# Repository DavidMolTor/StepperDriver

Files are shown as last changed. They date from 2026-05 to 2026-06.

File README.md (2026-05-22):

# STEPPER DRIVER

A simple stepper driver module using a Seeed Studio Xiao development board and TMC2209 stepper driver IC.

## Introduction

This module is designed to be used as a stepper controller for a testbench platform.

The design is centered around the ESP32-C6 XIAO development board from Seeed Studio. It can be soldered as an SMD part in order to have access to the driver debug wire and JTAG connector on the board.

Compatibility with other drivers like the TMC2208 could be possible, the footprints for the different package needs to be checked before attempting to use it.

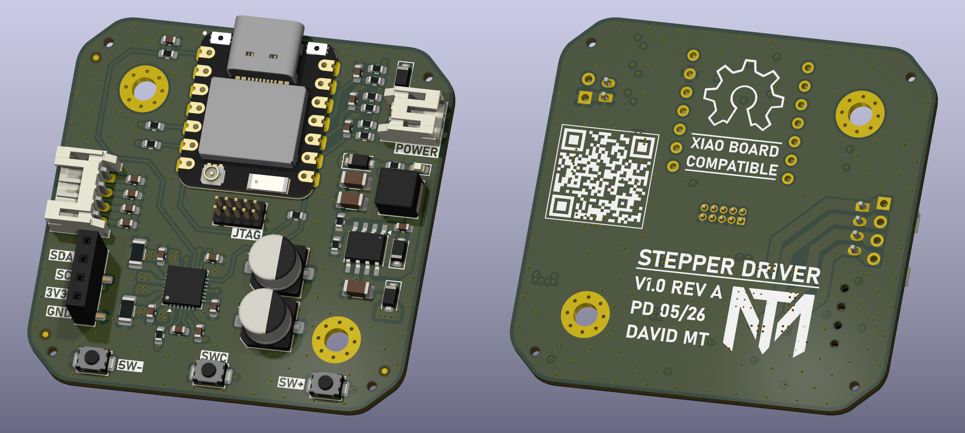
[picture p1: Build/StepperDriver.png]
STEPPER DRIVER


## Features

 - Wide input voltage range of 12-28V.

 - High current capability of up to 2.0A.

 - Wireless connectivity and LCD screen.

 - Afforable BOM with high quality parts.

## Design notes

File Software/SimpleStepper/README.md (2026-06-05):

| Supported Targets | ESP32-C6 |
| --- | --- |

# Simple Stepper Driver

Simple stepper driver using the TMC2209 in UART-controlled mode.

### Hardware Required

* XIAO ESP32-C6 development board
* TMC2209 stepper motor driver

### Configure the Project

TODO

### Build and Flash

Run `idf.py -p PORT flash monitor` to build, flash and monitor the project.

(To exit the serial monitor, type ``Ctrl-]``.)

See the [Getting Started Guide](https://docs.espressif.com/projects/esp-idf/en/latest/get-started/index.html) for full steps to configure and use ESP-IDF to build projects.

## Example Output

TODO

## Troubleshooting

TODO

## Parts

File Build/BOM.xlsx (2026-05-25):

Reference | Qty | Value | Footprint | Manufacturer Part | JLCPCB Part
C1,C2,C3,C8,C12,C13,C14,C15 | 8 | 100n | Capacitor_SMD:C_0603_1608Metric | CC0603KRX7R9BB104 | C14663
C4,C5 | 2 | 47u | Capacitor_SMD:CP_Elec_6.3x5.8 | SVZ1VM470E06E00RAXXX | C721322
C6,C18,C19,C20 | 4 | 10n | Capacitor_SMD:C_0603_1608Metric | 0603B103K500NT | C57112
C7 | 1 | 10u | Capacitor_SMD:C_1206_3216Metric | CL31A106KBHNNNE | C13585
C9,C10 | 2 | 22u | Capacitor_SMD:C_1206_3216Metric | CL31A226KAHNNNE | C12891
C11 | 1 | 22n | Capacitor_SMD:C_0603_1608Metric | CL10B223KB8NNNC | C21122
C16 | 1 | 2.2u | Capacitor_SMD:C_0603_1608Metric | CL10A225KO8NNNC | C23630
C17 | 1 | 1u | Capacitor_SMD:C_0603_1608Metric | CL10A105KB8NNNC | C15849
D1,D2,D4 | 3 | DSK24 | Diode_SMD:D_SOD-123F | DSK24 | C22466352
D3 | 1 | SMF40CA | Diode_SMD:D_SOD-123F | SMF40CA | C42371749
D5 | 1 | RED | LED_SMD:LED_0603_1608Metric | KT-0603R | C2286
L1 | 1 | 47u | Inductor_SMD:L_Changjiang_FNR5040S | FNR5040S470MT | C167974
R1,R3,R10,R11,R12,R14,R15,R16 | 8 | 10K | Resistor_SMD:R_0603_1608Metric | 0603WAF1002T5E | C25804
R2 | 1 | 3.3K | Resistor_SMD:R_0603_1608Metric | 0603WAF3301T5E | C22978
R4 | 1 | 22K | Resistor_SMD:R_0603_1608Metric | 0603WAF2202T5E | C31850
R5,R6 | 2 | 100m | Resistor_SMD:R_1206_3216Metric | 1206W4F100LT5E | C25334
R7,R8,R13 | 3 | 2.2K | Resistor_SMD:R_0603_1608Metric | 0603WAF2201T5E | C4190
R9 | 1 | 0R | Resistor_SMD:R_0603_1608Metric | 0603WAF0000T5E | C21189
SW1,SW2,SW3 | 3 | SPST_TS | Button_Switch_SMD:SW_SPST_TS-1088-xR020 | TS-1088-AR02016 | C720477
U1 | 1 | TPS5430DDA | Custom_Parts:TI_SO-PowerPAD-8_ThermalVias | TPS5430DDAR | C9864
U2 | 1 | TMC2209-LA | Custom_Parts:VQFN-28-1EP_5x5mm_P0.5mm_EP3.7x3.7mm_ThermalVias | TMC2209-LA-T | C2150710

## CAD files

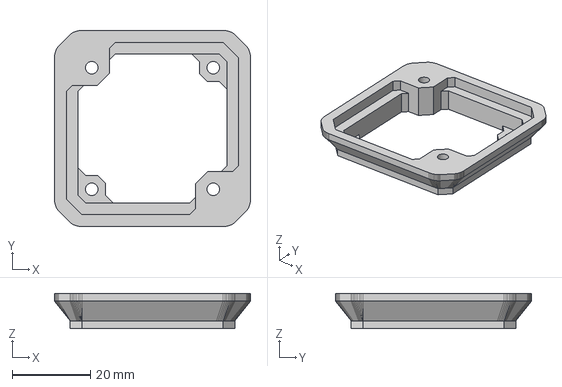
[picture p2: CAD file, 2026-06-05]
Build/Spacer.step
50.0 x 50.0 x 9.00 mm

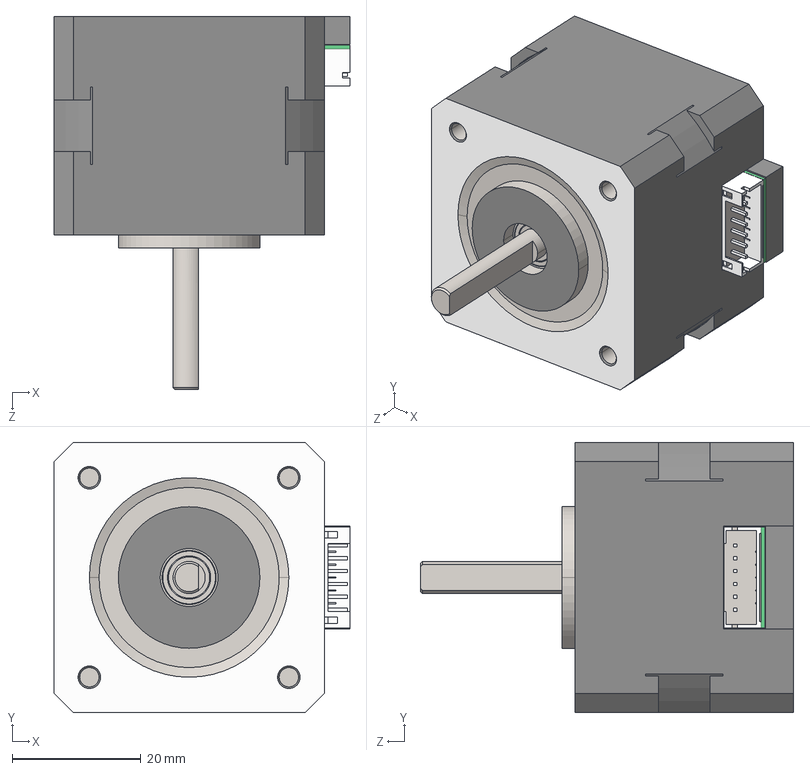
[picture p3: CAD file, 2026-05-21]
Build/Nema17.step
46.0 x 42.0 x 58.0 mm

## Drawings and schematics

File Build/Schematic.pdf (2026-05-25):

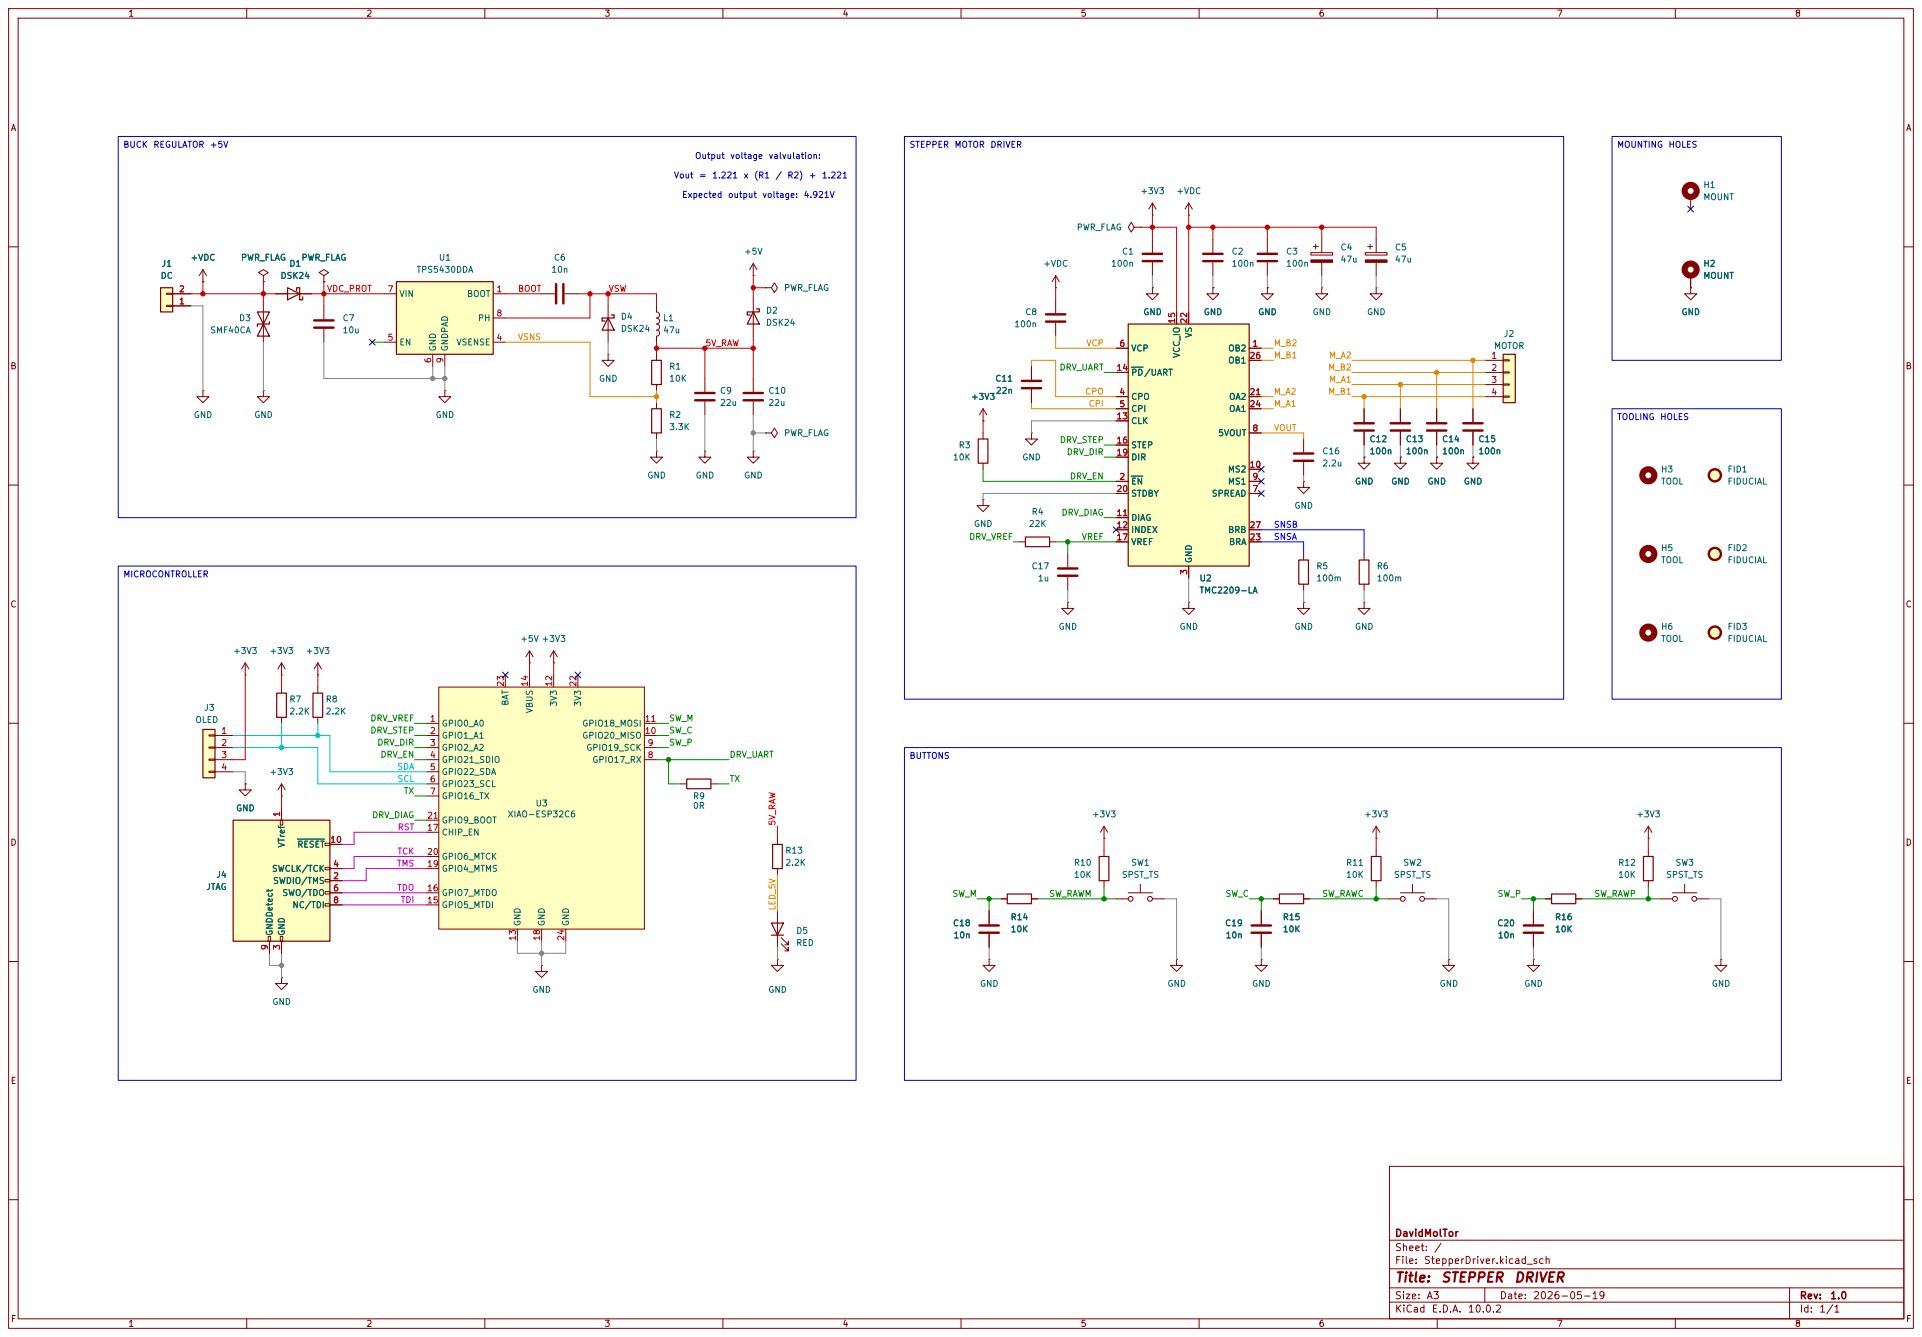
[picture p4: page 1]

Size: A3 | Rev: 1.0 | F Date: 2026-05-19
KiCad E.D.A. 10.0.2 | Id: 1/1

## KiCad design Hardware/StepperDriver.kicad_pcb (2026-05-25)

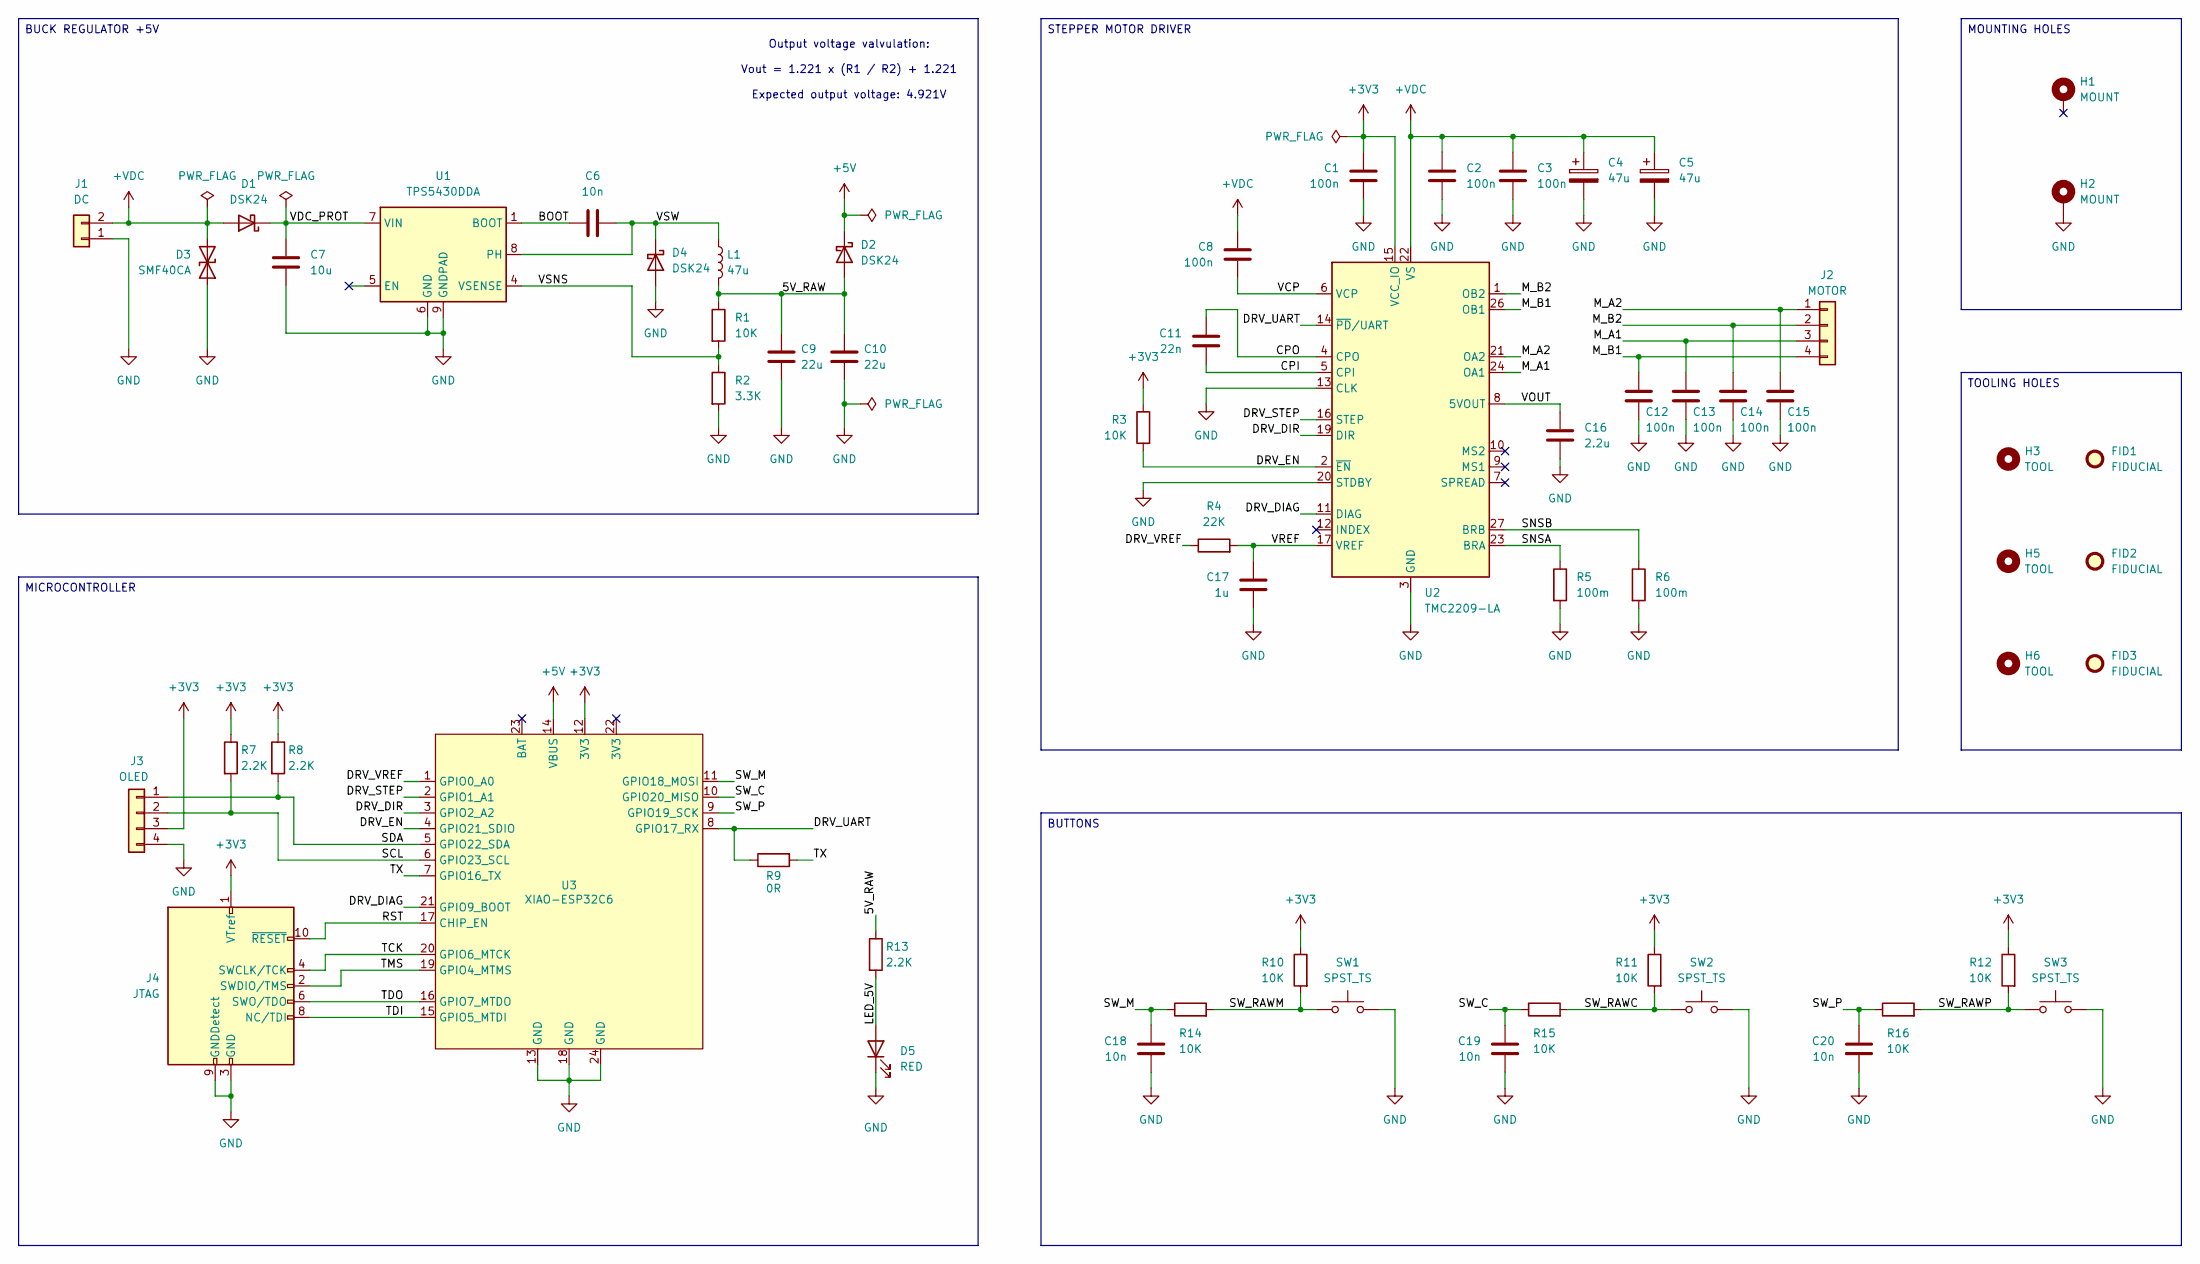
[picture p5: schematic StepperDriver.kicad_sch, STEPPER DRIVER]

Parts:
C1, C2, C3, C8, C12, C13, C14, C15: 100n; C_0603_1608Metric; Manufacturer Part CC0603KRX7R9BB104; JLCPCB Part C14663
C4, C5: 47u; CP_Elec_6.3x5.8; Manufacturer Part SVZ1VM470E06E00RAXXX; JLCPCB Part C721322
C6, C18, C19, C20: 10n; C_0603_1608Metric; Manufacturer Part 0603B103K500NT; JLCPCB Part C57112
C7: 10u; C_1206_3216Metric; Manufacturer Part CL31A106KBHNNNE; JLCPCB Part C13585
C9, C10: 22u; C_1206_3216Metric; Manufacturer Part CL31A226KAHNNNE; JLCPCB Part C12891
C11: 22n; C_0603_1608Metric; Manufacturer Part CL10B223KB8NNNC; JLCPCB Part C21122
C16: 2.2u; C_0603_1608Metric; Manufacturer Part CL10A225KO8NNNC; JLCPCB Part C23630
C17: 1u; C_0603_1608Metric; Manufacturer Part CL10A105KB8NNNC; JLCPCB Part C15849
D1, D2, D4: DSK24; D_SOD-123F; Manufacturer Part DSK24; JLCPCB Part C22466352
D3: SMF40CA; D_SOD-123F; Manufacturer Part SMF40CA; JLCPCB Part C42371749
D5: RED; LED_0603_1608Metric; Manufacturer Part KT-0603R; JLCPCB Part C2286
FID1, FID2, FID3: FIDUCIAL; Fiducial_0.75mm_Mask1.5mm
H1, H2: MOUNT; MountingHole_3.2mm_M3_Pad_Via
H3, H5, H6: TOOL; ToolingHole_1.152mm
J1: DC; JST_PH_S2B_1x02_COMBO; Manufacturer Part S2B-PH-K(LF)(SN); JLCPCB Part C265016
J2: MOTOR; JST_PH_S4B_1x04_COMBO; Manufacturer Part S4B-PH-K(LF)(SN); JLCPCB Part C265452
J3: OLED; HEADER_THROUGH_1x04_P2.54mm
J4: JTAG; PinHeader_2x05_P1.27mm_Vertical
L1: 47u; L_Changjiang_FNR5040S; Manufacturer Part FNR5040S470MT; JLCPCB Part C167974
R1, R3, R10, R11, R12, R14, R15, R16: 10K; R_0603_1608Metric; Manufacturer Part 0603WAF1002T5E; JLCPCB Part C25804
R2: 3.3K; R_0603_1608Metric; Manufacturer Part 0603WAF3301T5E; JLCPCB Part C22978
R4: 22K; R_0603_1608Metric; Manufacturer Part 0603WAF2202T5E; JLCPCB Part C31850
R5, R6: 100m; R_1206_3216Metric; Manufacturer Part 1206W4F100LT5E; JLCPCB Part C25334
R7, R8, R13: 2.2K; R_0603_1608Metric; Manufacturer Part 0603WAF2201T5E; JLCPCB Part C4190
R9: 0R; R_0603_1608Metric; Manufacturer Part 0603WAF0000T5E; JLCPCB Part C21189
SW1, SW2, SW3: SPST_TS; SW_SPST_TS-1088-xR020; Manufacturer Part TS-1088-AR02016; JLCPCB Part C720477
U1: TPS5430DDA; TI_SO-PowerPAD-8_ThermalVias; Manufacturer Part TPS5430DDAR; JLCPCB Part C9864
U2: TMC2209-LA; VQFN-28-1EP_5x5mm_P0.5mm_EP3.7x3.7mm_ThermalVias; Manufacturer Part TMC2209-LA-T; JLCPCB Part C2150710
U3: XIAO-ESP32C6; XIAO-ESP32C6-SMD

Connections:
+3V3: C1.1, J3.3, J4.1 (VTref), R3.1, R7.1, R8.1, R10.1, R11.1, R12.1, U2.15 (VCC_IO), U3.12 (3V3)
+5V: D2.1 (K), U3.14 (VBUS)
+VDC: C2.1, C3.1, C4.1, C5.1, C8.1, D1.2 (A), D3.2 (A2), J1.2, U2.22 (VS), U2.28 (VS)
/5V_RAW: C9.1, C10.1, D2.2 (A), L1.2, R1.1, R13.1
/BOOT: C6.1, U1.1 (BOOT)
/CPI: C11.2, U2.5 (CPI)
/CPO: C11.1, U2.4 (CPO)
/DRV_DIAG: U2.11 (DIAG), U3.21 (GPIO9_BOOT)
/DRV_DIR: U2.19 (DIR), U3.3 (GPIO2_A2)
/DRV_EN: R3.2, U2.2 (~EN), U3.4 (GPIO21_SDIO)
/DRV_STEP: U2.16 (STEP), U3.2 (GPIO1_A1)
/DRV_UART: R9.1, U2.14 (~PD/UART), U3.8 (GPIO17_RX)
/DRV_VREF: R4.1, U3.1 (GPIO0_A0)
/LED_5V: D5.2 (A), R13.2
/M_A1: C13.1, J2.3, U2.24 (OA1)
/M_A2: C15.1, J2.1, U2.21 (OA2)
/M_B1: C12.1, J2.4, U2.26 (OB1)
/M_B2: C14.1, J2.2, U2.1 (OB2)
/RST: J4.10 (~RESET), U3.17 (CHIP_EN)
/SCL: J3.2, R7.2, U3.6 (GPIO23_SCL)
/SDA: J3.1, R8.2, U3.5 (GPIO22_SDA)
/SNSA: R5.1, U2.23 (BRA)
/SNSB: R6.1, U2.27 (BRB)
/SW_C: C19.1, R15.1, U3.10 (GPIO20_MISO)
/SW_M: C18.1, R14.1, U3.11 (GPIO18_MOSI)
/SW_P: C20.1, R16.1, U3.9 (GPIO19_SCK)
/SW_RAWC: R11.2, R15.2, SW2.1
/SW_RAWM: R10.2, R14.2, SW1.1
/SW_RAWP: R12.2, R16.2, SW3.1
/TCK: J4.4 (SWCLK/TCK), U3.20 (GPIO6_MTCK)
/TDI: J4.8 (NC/TDI), U3.15 (GPIO5_MTDI)
/TDO: J4.6 (SWO/TDO), U3.16 (GPIO7_MTDO)
/TMS: J4.2 (SWDIO/TMS), U3.19 (GPIO4_MTMS)
/TX: R9.2, U3.7 (GPIO16_TX)
/VCP: C8.2, U2.6 (VCP)
/VDC_PROT: C7.1, D1.1 (K), U1.7 (VIN)
/VOUT: C16.1, U2.8 (5VOUT)
/VREF: C17.1, R4.2, U2.17 (VREF)
/VSNS: R1.2, R2.1, U1.4 (VSENSE)
/VSW: C6.2, D4.1 (K), L1.1, U1.8 (PH)
GND: C1.2, C2.2, C3.2, C4.2, C5.2, C7.2, C9.2, C10.2, C12.2, C13.2, C14.2, C15.2, C16.2, C17.2, C18.2, C19.2, C20.2, D3.1 (A1), D4.2 (A), D5.1 (K), H2.1 (1_1), J1.1, J3.4, J4.3 (GND), J4.5 (GND), J4.9 (GNDDetect), R2.2, R5.2, R6.2, SW1.2, SW2.2, SW3.2, U1.6 (GND), U1.9 (GNDPAD), U2.3 (GND), U2.13 (CLK), U2.18 (GND), U2.20 (STDBY), U2.29 (GND), U3.13 (GND), U3.18 (GND), U3.24 (GND)

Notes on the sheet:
Output voltage valvulation: Vout = 1.221 x (R1 / R2) + 1.221 Expected output voltage: 4.921V
TOOLING HOLES
MICROCONTROLLER
MOUNTING HOLES
BUTTONS
BUCK REGULATOR +5V
STEPPER MOTOR DRIVER

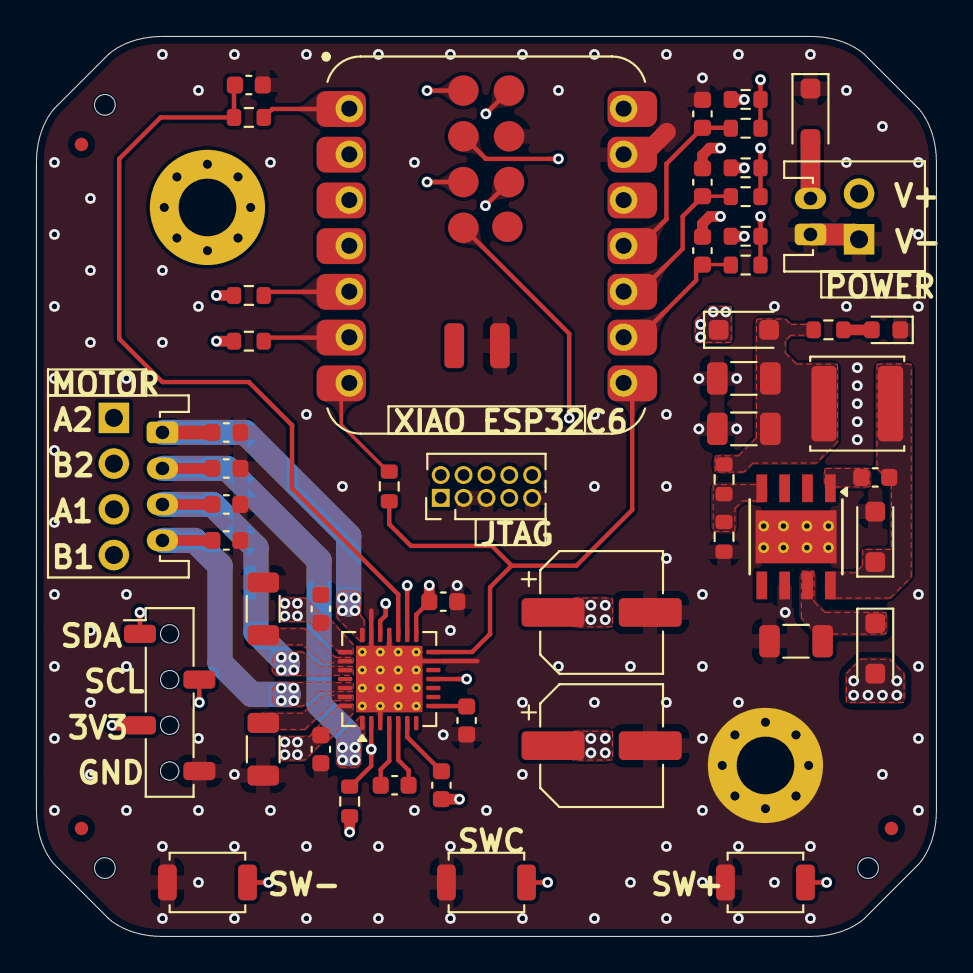
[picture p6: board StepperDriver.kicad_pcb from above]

Board: 6 copper layers, 50.0 x 50.0 mm, 60 parts (0 on the bottom side), 41 nets.

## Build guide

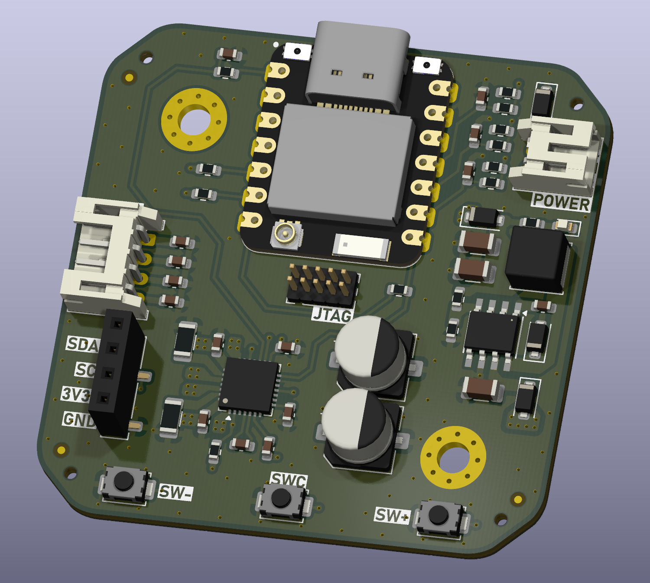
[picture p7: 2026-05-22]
Build/Front.png

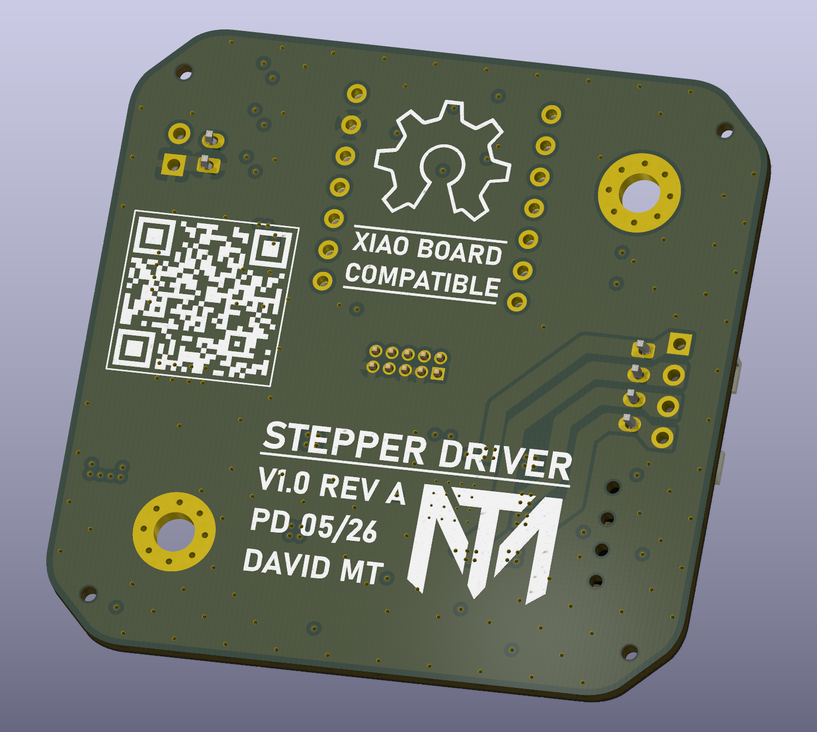
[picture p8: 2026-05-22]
Build/Back.png

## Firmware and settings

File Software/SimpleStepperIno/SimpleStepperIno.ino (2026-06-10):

#include <TMC2209.h>

// Instantiate TMC2209 driver
TMC2209 stepper_driver;

// Serial stream object declaration
HardwareSerial& serial_stream = Serial0;

// Stepper driver UART definitions
#define UART_SERIAL_PORT  TMC2209::SERIAL_ADDRESS_0
#define UART_BAUD_RATE    115200
#define UART_RX_PIN       17
#define UART_TX_PIN       16

// Stepper driver pin definitions
#define STP_PIN   1
#define DIR_PIN   2
#define EN_PIN    21

// TMC2209 current control definitions
#define RMS_CURRENT_VALUE   200.0f
#define EXT_RESISTOR_VALUE  0.1f

// Value definitions for the NEMA17
#define STEPS_PER_REV       200.0f
#define MAX_RPM             600.0f
#define RPM_STEPPING        60.0f
#define MAX_USTEPS          8

// GPIO pin definitions
#define SWM_PIN 18
#define SWC_PIN 20
#define SWP_PIN 19

static uint32_t step_delay_us     = 0;
static uint8_t current_microstep  = 0;

static float current_speed_rpm    = 0.0f;
static float target_speed_rpm     = 60.0f;
static float accel_rpm_per_s      = 15.0f;

static long last_ramp_update      = 0;

static uint32_t rpm_to_step_delay_us(float rpm, uint8_t microstep) {
  if (rpm <= 0.0f) {
    return 0;
  }

  if (rpm > MAX_RPM) {
    rpm = MAX_RPM;
  }

  float steps_per_rev = STEPS_PER_REV * (float)(2 ^ microstep);
  float steps_per_sec = (rpm * steps_per_rev) / 60.0f;

  if (steps_per_sec < 1.0f) {
    steps_per_sec = 1.0f;
  }

  return (uint32_t)(1000000.0f / steps_per_sec);
}

static void stepper_apply_speed() {
  step_delay_us = rpm_to_step_delay_us(current_speed_rpm, current_microstep);
}

static void stepper_set_direction(bool clockwise) {
  digitalWrite(DIR_PIN, clockwise ? HIGH : LOW);
}

static void stepper_set_speed_rpm(float rpm) {
  if (rpm < 0.0f) {
    rpm = 0.0f;
  }

  if (rpm > MAX_RPM) {
    rpm = MAX_RPM;
  }

  target_speed_rpm = rpm;
}

static void stepper_set_acceleration_rpm(float rpm_per_s) {
  if (rpm_per_s < 1.0f) {
    rpm_per_s = 1.0f;
  }

  accel_rpm_per_s = rpm_per_s;
}

static void stepper_update_speed_ramp(void) {
  long now = micros();
  int64_t dt_us = now - last_ramp_update;
  last_ramp_update = now;

  if (dt_us <= 0) {
    return;
  }

  float dt_s = (float)dt_us / 1000000.0f;
  float max_delta_rpm = accel_rpm_per_s * dt_s;
  float error = target_speed_rpm - current_speed_rpm;

  if (fabsf(error) <= max_delta_rpm) {
    current_speed_rpm = target_speed_rpm;
  } else if (error > 0.0f) {
    current_speed_rpm += max_delta_rpm;
  } else {
    current_speed_rpm -= max_delta_rpm;
  }

  stepper_apply_speed();
}

static void stepper_run(void) {
  stepper_update_speed_ramp();

  if (step_delay_us == 0) {
    delayMicroseconds(1000);
    return;
  }

  digitalWrite(STP_PIN, HIGH);
  delayMicroseconds(2);
  digitalWrite(STP_PIN, LOW);

  if (step_delay_us > 2) {
    delayMicroseconds(step_delay_us - 2);
  }
}

static void gpioCallback() {
  if (digitalRead(SWM_PIN) == LOW) {
    target_speed_rpm -= RPM_STEPPING;

    if (target_speed_rpm < 0.0f)
      target_speed_rpm = 0;
  }

  if (digitalRead(SWC_PIN) == LOW) {
    current_microstep++;

    if (current_microstep > MAX_USTEPS)
      current_microstep = 0;
  }

  if (digitalRead(SWP_PIN) == LOW) {
    target_speed_rpm += RPM_STEPPING;

    if (target_speed_rpm > MAX_RPM)
      target_speed_rpm = MAX_RPM;
  }

  stepper_set_speed_rpm(target_speed_rpm);
  stepper_apply_speed();

  Serial.print("Motor speed / microsteps: ");
  Serial.print(target_speed_rpm);
  Serial.print(" / ");
  Serial.println(current_microstep);
}

void setup() {
  // Set the step pin configuration
  pinMode(STP_PIN, OUTPUT);
  digitalWrite(STP_PIN, LOW);

  // Set the direction pin configuration
  pinMode(DIR_PIN, OUTPUT);
  digitalWrite(DIR_PIN, LOW);

  // Set the enable pin configuration
  pinMode(EN_PIN, OUTPUT);
  digitalWrite(EN_PIN, LOW);

  // Set the switch configurations
  pinMode(SWM_PIN, INPUT);
  pinMode(SWC_PIN, INPUT);
  pinMode(SWP_PIN, INPUT);
  attachInterrupt(digitalPinToInterrupt(SWM_PIN), gpioCallback, FALLING);
  attachInterrupt(digitalPinToInterrupt(SWC_PIN), gpioCallback, FALLING);
  attachInterrupt(digitalPinToInterrupt(SWP_PIN), gpioCallback, FALLING);

  delay(100);

  // Initialize the serial port
  Serial.begin(UART_BAUD_RATE);
  delay(100);

  // Setup the TMC2209 stepper driver
  stepper_driver.setup(serial_stream, UART_BAUD_RATE, UART_SERIAL_PORT, UART_RX_PIN, UART_TX_PIN);
  delay(100);

  // CHeck if the driver is setup and working
  if (stepper_driver.isSetupAndCommunicating()) {
    // Enable the stepper driver
    stepper_driver.enable();

    // Set the initial configuration
    stepper_driver.useExternalSenseResistors();
    stepper_driver.enableCoolStep();
    stepper_driver.setMicrostepsPerStep(current_microstep);

    // Set the current control configuration
    stepper_driver.setRMSCurrent(RMS_CURRENT_VALUE, EXT_RESISTOR_VALUE);
    stepper_driver.enableAutomaticCurrentScaling();
    stepper_driver.enableAutomaticGradientAdaptation();

    // Set the initial direction
    stepper_set_direction(true);

    // Set the initial update time
    last_ramp_update = micros();

    Serial.println("Stepper driver running...");
  } else {
    Serial.println("Stepper driver setup error!");
  }
}

void loop() {
  // Execute the stepper control
  stepper_run();
}

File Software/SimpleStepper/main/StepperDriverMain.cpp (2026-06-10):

#include <cstdio>
#include <cstring>

#include "freertos/FreeRTOS.h"
#include "freertos/task.h"

#include "driver/gpio.h"
#include "driver/usb_serial_jtag.h"
#include "driver/usb_serial_jtag_vfs.h"

#include "sdkconfig.h"

#include "ManagerWifi.h"
#include "ManagerOTA.h"

#include "TMC2209.h"

// User accessible LED GPIO definition
#define USER_LED_GPIO (gpio_num_t)CONFIG_USER_LED_GPIO

// TMC2209 driver pin definitions
#define TMC2209_VREF_GPIO    (gpio_num_t)CONFIG_TMC2209_VREF_GPIO
#define TMC2209_STEP_GPIO    (gpio_num_t)CONFIG_TMC2209_STEP_GPIO
#define TMC2209_DIR_GPIO     (gpio_num_t)CONFIG_TMC2209_DIR_GPIO
#define TMC2209_EN_GPIO      (gpio_num_t)CONFIG_TMC2209_EN_GPIO
#define TMC2209_RX_GPIO      (gpio_num_t)CONFIG_TMC2209_RX_GPIO
#define TMC2209_TX_GPIO      (gpio_num_t)CONFIG_TMC2209_TX_GPIO
#define TMC2209_DIAG_GPIO    (gpio_num_t)CONFIG_TMC2209_DIAG_GPIO

// TMC2209 serial address definition
#define TMC2209_SERIAL_ADDRESS 0

// I2C bus pin definitions
#define I2C_SDA_GPIO CONFIG_I2C_SDA_GPIO
#define I2C_SCL_GPIO CONFIG_I2C_SCL_GPIO

// Board switches pin definitions
#define SWM_GPIO CONFIG_SWM_GPIO
#define SWC_GPIO CONFIG_SWC_GPIO
#define SWP_GPIO CONFIG_SWP_GPIO

// NEMA17 specification definitions
#define STEPS_PER_REV   200
#define CURRENT_RMS_MA  1000

static void init_console()
{
    usb_serial_jtag_driver_config_t cfg = {
        .tx_buffer_size = 256,
        .rx_buffer_size = 256,
    };
    ESP_ERROR_CHECK(usb_serial_jtag_driver_install(&cfg));

    usb_serial_jtag_vfs_use_driver();

    usb_serial_jtag_vfs_set_rx_line_endings(ESP_LINE_ENDINGS_CR);
    usb_serial_jtag_vfs_set_tx_line_endings(ESP_LINE_ENDINGS_CRLF);

    setvbuf(stdin, NULL, _IONBF, 0);
    setvbuf(stdout, NULL, _IONBF, 0);
    setvbuf(stderr, NULL, _IONBF, 0);
}

static void init_gpio()
{
    // Configure the user LED
    gpio_reset_pin(USER_LED_GPIO);
    gpio_set_direction(USER_LED_GPIO, GPIO_MODE_OUTPUT);
    gpio_set_level(USER_LED_GPIO, 1);

    // Default button configuration
    gpio_config_t io_conf = {
        .pin_bit_mask   = 1ULL,
        .mode           = GPIO_MODE_INPUT,
        .pull_up_en     = GPIO_PULLUP_DISABLE,
        .pull_down_en   = GPIO_PULLDOWN_DISABLE,
        .intr_type      = GPIO_INTR_DISABLE
    };

    // Configure each button
    io_conf.pin_bit_mask = 1ULL << CONFIG_SWM_GPIO;
    ESP_ERROR_CHECK(gpio_config(&io_conf));
    io_conf.pin_bit_mask = 1ULL << CONFIG_SWC_GPIO;
    ESP_ERROR_CHECK(gpio_config(&io_conf));
    io_conf.pin_bit_mask = 1ULL << CONFIG_SWP_GPIO;
    ESP_ERROR_CHECK(gpio_config(&io_conf));    
}

static void run_maintenance(ManagerWifi &wifi, ManagerOTA &ota)
{
    ota.startServiceMDNS();
    ota.startWebServer();

    while (true) {
        printf("OTA web server active, waiting for firmware...\n");
        vTaskDelay(pdMS_TO_TICKS(1000));
    }
}

static void run_app(ManagerWifi &wifi)
{
    TMC2209 stepper_driver;

    stepper_driver.setGPIO(TMC2209_EN_GPIO, TMC2209_STEP_GPIO, TMC2209_DIR_GPIO);
    vTaskDelay(pdMS_TO_TICKS(100));

    stepper_driver.setup(UART_NUM_0, TMC2209_TX_GPIO, TMC2209_RX_GPIO, TMC2209_SERIAL_ADDRESS);
    vTaskDelay(pdMS_TO_TICKS(100));
    
    while (true) {
        printf("Driver status: %d\n", stepper_driver.getConnected());
        printf("Main app running...\n");
        vTaskDelay(pdMS_TO_TICKS(10000));
    }
}

extern "C" void app_main(void)
{
    init_console();
    init_gpio();

    // Manager definitions
    ManagerWifi managerWifi;
    ManagerOTA managerOTA(SWC_GPIO, USER_LED_GPIO);

    // Check for OTA button
    bool ota_mode = managerOTA.isOtaButtonPressed();

    // Initialize the wifi
    managerWifi.init();

    // Check for saved credentials
    ManagerWifi::Credentials credentials;
    do
    {
        if (!managerWifi.hasSavedCredentials()) {
            credentials = managerWifi.serialProvisioning();
        } else {
            credentials = managerWifi.loadCredentials();
        }
    } while (!credentials.valid());

    // Connect to the given wifi network
    if (!managerWifi.connect(credentials) && ota_mode) {
        do
        {
            credentials = managerWifi.serialProvisioning();
        } while (!managerWifi.connect(credentials));
    }
    
    // Run OTA mode if requested
    if (ota_mode) {
        run_maintenance(managerWifi, managerOTA);
    } else {
        run_app(managerWifi);
    }
}

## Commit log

2026-05-19 Project files
    Added the KiCAD project files.
    Added a readme file.
    Added a license file.
    Added a gitignore file.
    [StepperDriver.kicad_pcb, StepperDriver.kicad_sch]
2026-05-20 Initial schematic
    Completed the first iteration for the schematic.
    Included a default 42x42mm PCB area.
    [StepperDriver.kicad_pcb, StepperDriver.kicad_sch]
2026-05-21 Initial layout
    Completed the first iteration for the layout.
    Increased the PCB area to 50x50mm.
    Minor changes in the schematic.
    [StepperDriver.kicad_pcb, StepperDriver.kicad_sch]
2026-05-21 Initial ESP32C6 layout
    Moved to a XIAO ESP32C6 development board.
    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
    [StepperDriver.kicad_pcb, StepperDriver.kicad_sch]
2026-05-21 Build output files
    Generated the output files for the first iteration of the ESP32-C6 board.
    Added some board images and 3D model.
    Added the BOM and POS files for assembly.
    [BOM.xlsx, StepperDriver.kicad_pcb, StepperDriver.kicad_sch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]
2026-05-21 Assembly revision
    Minor changes to the board and schematic.
    Updated the output files.
    [BOM.xlsx, StepperDriver.kicad_pcb, StepperDriver.kicad_sch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]
2026-05-21 File names
    Updated some of the names for the output files.
    [StepperDriver.kicad_pcb]
2026-05-21 Build output files
    Rounded the corners of the board.
    Updated the output files and added a spacer model.
    [Nema17.step, Spacer.step, StepperDriver.kicad_pcb]
2026-05-22 Driver update
    Moved to the better TMC2209 stepper motor driver.
    Added a status LED for the voltage regulator.
    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
    [BOM.xlsx, Spacer.step, StepperDriver.kicad_pcb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]
2026-05-22 Output files
    Minor changes on the PCB.
    Updated the bulk capacitors for the board to have a lower voltage rating.
    [BOM.xlsx, StepperDriver.kicad_pcb, StepperDriver.kicad_sch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]
2026-05-23 Output files
    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
    [BOM.xlsx, StepperDriver.kicad_pcb, StepperDriver.kicad_sch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]
2026-05-25 Assembly review
    Performed a full review of the schematic and layout.
    Minor changes to the schematic and layout.
    Updated output files.
    [BOM.xlsx, StepperDriver.kicad_pcb, StepperDriver.kicad_sch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]
2026-06-05 Initial control software
    Added a basic Arduino program to control the speed of the motor via UART named BasicStepper.
    Added the initial driver for the board named SimpleStepper.
    [Spacer.step]
2026-06-05 Basic driver upgrade
    Upgraded the basic Arduino code so that the speed and microstepping can be controlled using the onboard buttons.
2026-06-05 Simple Arduino drivers
    Updated the basic Arduino motor driver code.
    Added a new driver using the step and direction pin with the Arduino libraries.
2026-06-10 Stepper driver software
    Unified the basic and simple driver Arduino code.
    Updated the ESP-IDF prior to adding the TMC2209 driver class.
2026-06-10 TMC2209 driver class
    Added the driver class for the TMC2209.
    Revieww the UART communication between the MCU and the stepper driver.
2026-06-10 TCM2209 driver UART
    Updated the UART comms for the TMC2209.
    Success on testing the TCM2209 initial setup via UART.
